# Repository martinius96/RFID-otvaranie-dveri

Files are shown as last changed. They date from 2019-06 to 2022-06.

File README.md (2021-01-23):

# RFID vrátnik s mikrokontrolérom ESP8266, ESP32
# Podporte projekt pre pridanie nových funkcionalít
* https://www.paypal.me/chlebovec
# Stránka projektu
* Informácie o projekte: http://arduino.clanweb.eu/rfid-system.php 
* Testovacie webové rozhranie: http://arduino.clanweb.eu/rfid/
* **Z dostupných zdrojových kódov pre platformy Arduino, ESP8266 a ESP32 je možné využiť iba HTTP variant, nakoľko freehosting clanweb.eu nemá podporu HTTPS!**
* Možnosť ihneď vyskúšať funkcionalitu systému v testovacom webovom rozhraní po zapojení čítačky NXP RC522 a nahratí programu pre odtestovanie funkčnosti
* Čítačka RC522 funguje na frekvencii 13.56 MHz, dokáže prečítať RFID tagy štandardu ISO/IEC 14443-A
* Webové rozhranie dokáže vizualizovať priloženia karty historicky s výsledkom overenia s možnosťou riadenia prístupu - autorizácie / deautorizácie kariet (automatická obnova údajov bola odstránená)
* Vhodné ako základ pre vlastný projekt s RFID vstupom od používateľa
* Pridaná podpora pre Over The Air aktualizáciu firmvéru prostredníctvom LAN siete - Basic OTA cez Python z prostredia Arduino IDE
* **Čítačka Wiegand, RDM6300 nie je dostupná vo free verzii projektu RFID vrátnik**
* Článok k projektu (verzia 1.0): https://chiptron.cz/articles.php?article_id=216

# Systém ponúka 2 typy užívateľov projektu
| Administrátor:  | Používateľ:  |
| --- | --- |
| Spravuje webové rozhranie | Fyzicky prikladá NFC tag/kľúčenku/náramok/kartu|
| V reálnom čase vidí priloženie karty s výsledkom overenia  | Pri overeni sú mu odistené dvere na 5 sekúnd|
| Historicky vidí 100 posledných priložení  | Pri neoverení používateľa sa jazýček nevtiahne  |
| Jedným kliknutím môže schváliť už (skôr) priloženú kartu  | Používateľ o overení/neoverení nie je informovaný (led/buzzer)|
| Odstránenie karty jedným kliknutím  |  Používateľ použije Mifare tag, bankomatovú kartu, ISIC kartu, náramok, ktorý spĺňa štandard ISO/IEC 14443 A |
| Grafická reprezentácia prístupov  | |
| Štatistika RFID vrátnika  |  |
| Vidí zdrojový kód pre mikrokontroléry  |  |

* Mikrokontróler po prečítaní UID (identifikátor, ktorý vysiela) RFID karty prostredníctvom čítačky odošle HTTP (HTTPS) POST request na webové rozhranie
* Webserver overí, či je karta medzi autorizovanými a odpovie textom OK, prípadne NO.
* Mikrokontróler na tento payload zareaguje a odistí dvere prostredníctvom solenoidu, ktorý je ovládaný cez 5V relé
* Z vnútornej strany objektu je možné dvere kľúčkou otvoriť, elektromagnetický jazýček (solenoid) sa vtiahne pri stlačení kľučky (1-cestný RFID vrátnik)
* Možno použiť Mifare tagy, ISIC karty, bankomatové, zamestnanecké karty, náramky i kľúčenky, ktoré spĺňajú štandard ISO/IEC 14443-A
* Mikrokontróler UID upraví, nikdy neodosiela pôvodný identifikátor karty, ktorý načíta.
* Na UART rozhranie mikrokontróler posiela udalosti - Eventy - priloženie karty s výsledkom overenia (akceptácie karty webserverom)
* UID sa ukladajú do MySQL databázy, existujú rôzne tabuľky - prístupy, autorizované karty, evidencia mien ku kartám...

# Hardvér
* NodeMCU**NodeMCU (v2, alebo v3)**
* BasekitBasekit (možný iba pri V3, možnosť využiť externé napájanie na 6-24V)
#
* Arduino Uno**Arduino Uno**
* Ethernet W5100Ethernet Wiznet W5100
* Ethernet W5500Ethernet Wiznet W5500
#
* ESP32 DevKit**ESP32 DevKit V1 / DevKitC V4**
#
* RC522Čítačka RC522 na 13.56 MHz pre štandard ISO/IEC 14443 A
* 13.56MHzKompatibilné karty a kľúčenky
* 1-kanálové elmg. reléSRD-05VDC-SL-C (elmg. relé 1-kanálové)
* Solenoidový jazýčekSolenoid - jazýčkový zámok

# Princíp solenoid jazýčka 
Princíp jazýčka

# Technológie
* HTML5
* PHP
* 
* 
* 
* Arduino core
* 

# Získanie Root CA certifikátu - (Pre ESP32 - HTTPS):
* openssl s_client -showcerts -verify 5 -connect example.com:443 < /dev/null
# Získanie SHA1 fingerprintu certifikátu - (Pre ESP8266 - HTTPS):
* openssl s_client -connect example.com:443 -showcerts < /dev/null 2>/dev/null   | openssl x509 -in /dev/stdin -sha1 -noout -fingerprint

# Inštalácia systému - krok po kroku
* Stiahnuť repozitár v .zip archíve z Githubu
* Súbor priečinka sql importovať do vašej MySQL databázy - štruktúru, alebo štruktúru + vzorové dáta
* V súbore connect.php nastaviť vaše údaje na databázu (umiestnenie (localhost/external), user, heslo, meno_db)
*  **(Win 10)** src priečinok skopírovať do: C:/Moje Dokumenty/Arduino/libraries/rfid
*  **(Win XP/Vista/7)** src priečinok skopírovať do: C:/Program Files/Arduino/libraries/rfid
* Web súbory nahrať na FTP server (kompatibilné s PHP 5, aj PHP 7)
* V zdrojovom kóde pre NodeMCU - zvoliť si verziu HTTPS/HTTP, zmeniť údaje k wifi sieti, údaje na váš webserver, rovnako i pre ESP32/Arduino
* Nahrať program, používať Arduino core 2.5.0/2.5.2 (pre NodeMCU), **verzia 2.3.0 (doteraz používaná) je nekompatibilná** pre HTTPS fingerprint!
* Pre Arduino, ESP32 je možné použiť aj nanovšie knižnice pre HTTP, HTTPS spojenia
* Program pre Arduino je plne kompatibilný medzi Arduino Uno, Nano, Mega 1280/2560
* Hotovo

# Webové rozhranie v prevádzke:
* Hlavný prehľad (real-time vstupy s výsledkom overenia)
Hlavný prehľad
* Pridanie autorizovaných kariet jedným kliknutím
Pridanie autorizovaných kariet jedným kliknutím
* Štatistika RFID vrátnika
Štatistika RFID vrátnika

# Zapojenie komponentov (Arduino)
| RC522 | Arduino |
|:-----|---:|
| 3.3V | 3.3V |
| RST  | D5 |
| GND  | GND |
| MISO | D12 |
| MOSI | D11 |
| SCK  | D5 |
| SDA/SS  | D6 |
| IRQ  | Nezapája sa |

| Relé | Arduino |
|:-----|---:|
| 5V | 5V  |
| GND  | GND |
| IN  | D3 |

# Zapojenie komponentov (NodeMCU)
| RC522 | NodeMCU |
|:-----|---:|
| 3.3V | 3.3V |
| RST  | D1 (GPIO5) |
| GND  | GND |
| MISO | D6 (GPIO12) |
| MOSI | D7 (GPIO13) |
| SCK  | D5 (GPIO14) |
| SDA/SS  | D2 (GPIO4) |
| IRQ  | Nezapája sa |

| Relé | NodeMCU |
|:-----|---:|
| 5V | VIN / VUSB (Adaptér/USB napájanie)  |
| GND  | GND |
| IN  | D0 (GPIO16) |

# Zapojenie komponentov (ESP32)
| RC522 | ESP32 |
|:-----|---:|
| 3.3V | 3.3V |
| RST  | D22 |
| GND  | GND |
| MISO | D19 |
| MOSI | D23 |
| SCK  | D18 |
| SDA/SS  | D21 |
| IRQ  | Nezapája sa |

| Relé | ESP32 |
|:-----|---:|
| 5V | 5V VIN  |
| GND  | GND |
| IN  | D17 |

# Zapojenie relé a solenoid jazyčkového zámku
| Relé | Solenoid |
|:-----|---:|
| NO | IN |
| COM  | - |
| NC  | 12/24 DC/AC |

* Nulák, respektíve GND podľa typu obvodu (AC/DC) je pripojený na zdroj po celú dobu prevádzky solenoid jazýčka.

# Schéma zapojenia Arduino
Schéma Arduino + Ethernet - RFID vrátnik

# Schéma zapojenia ESP8266 (NodeMCU)
Schéma NodeMCU - ESP8266 - RFID vrátnik

# Schéma zapojenia ESP32
Schéma ESP32 - RFID vrátnik

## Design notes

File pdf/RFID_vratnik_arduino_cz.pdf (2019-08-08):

# RFID SYSTÉM S ON-LINE SPRÁVOU V REÁLNOM ČASE

- 5.2.2019 ZBYŠEK VODA (https://arduino.cz/author/zbysekvoda/) ČLÁNKY, (https://arduino.cz/category/novinky/) ZAČÁTEČNÍK (https://arduino.cz/category/urovne/zacatecnik/) RFID (https://arduino.cz/tag/rfid/)

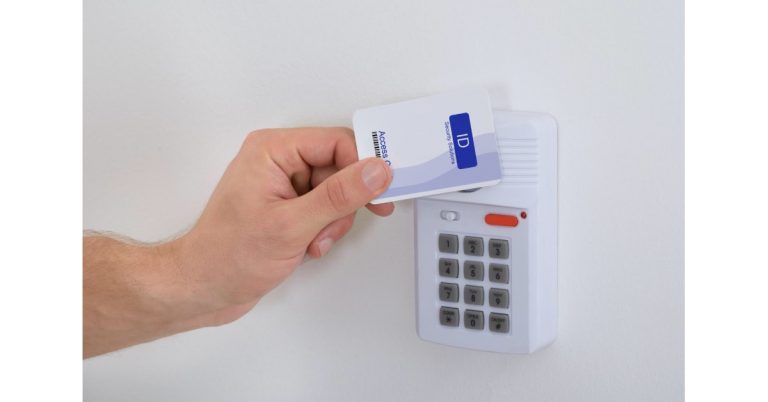
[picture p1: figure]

Ve dnešním článku se podíváme na přístupový systém založený na RFID kartách od našeho fanouška s přezdívkou martinius96.

Hledat … | H L E D A T
ÚVOD (https://arduino.cz/) | FÓRUM (https://www.arduino-forum.cz/) | ČLÁNKY (https://arduino.cz/category/novinky/) | CO JE TO ARDUINO? (https://arduino.cz/co-je-to-arduino/) | NÁVODY (https://arduino.cz/category/novinky/tutorialy/) | VIDEA (https://arduino.cz/category/videa/) | KOUPIT (https://www.hwkitchen.cz/arduino/)
Create PDF in your applications with the Pdfcrowd HTML to PDF API (https://pdfcrowd.com/doc/api/?ref=pdf) | PDFCROWD (https://pdfcrowd.com/?ref=pdf)

Zdar bastlíři, dnes by som rád predstavil systém, ktorý som vyvíjal pred niekoľkými mesiacmi.

Vyhotovil som RFID systém na otváranie dverí s elektomagnetickým jazýčekom na základe overenia užívateľa po priložení karty s takmer okamžitou odpoveďou. Systém je postavený na komponentoch pre Arduino, teda čítačka kariet a kľúčeniek na 13.56MHz RC522, kompatibilné karty a kľúčenky, relé. Tieto komponenty sú plne (https://www.hwkitchen.cz/rc522-rfid-ctecka-klicenka-a-karta/) kompatibilné aj s ESP modulmi. Rozhodol som sa pre NodeMCU s wi čipom ESP8266. (https://www.hwkitchen.cz/nodemcu-v3-esp8266-lua-wifi-ch340g/) Čítačka RC522 dokáže prečítať karty štandardu ISO/IEC 14443 A. Tento štandard funguje i na ISIC, bankomatové, autobusové, či zamestnanecké karty a je ich možné taktiež prečítať a využiť pre takýto projekt bez nutnosti investovať do nových kariet, či menších kľúčeniek. RC522 podporuje SPI zbernicu, po ktorej komunikuje s mikrokontrolérom.

## Aký je princíp funkčnosti tohto systému?

Čítačkou čítam MAC adresy kariet, ktoré si prevádzam na špecický decimálny formát (0-9 na každú pozíciu). Obsah karty sa nečíta! V úlohe mikrokontroléru pre spracovanie a odosielanie dát som použil dosku NodeMCU v3 Lolin, ktorá disponuje wi konektivitou, podporuje šifrovaný prenos a je pre tento účel je viac než dostačujúca.

Úlohou NodeMCU je odosielať dáta na web backend vždy, keď zaznamená kartu a na základe návratovej HTTP hlavičky určí podľa odpovede z webservera, či je užívateľovi povolený prístup. Dvere otvorí, alebo neotvorí, záznam s výsledkom si uloží do logu. Vo dverách sa okrem klasického mechanizmu s kľučkou nachádza i špeciálny elmg. jazýček, ktorý otvára mikrokontrolér na určitú dobu po úspešnej odpovedi z webservera. Funguje rovnako ako solenoid ventil. Nakoľko je na 5V a vyžaduje väčší prúd, využil som elektomagnetické relé na 3.3V so spínacím prúdom od 10mA (NodeMCU dáva 12mA na výstup), ktorým spínam mechanizmus jazýčka. Z vonkajšej strany dverí je guľa, z druhej strany kľučka, ktorá je prepojená i na jazýček. Z tohto dôvodu teda nie je nutné inštalovať dve čítačky, overuje sa iba užívateľ vchádzajúci do objektu.

Dáta sa odosielajú na server a spracúvajú sa na strane webservera v jazyku PHP. Všetky karty, ktoré boli kedy priložené sú archivované v MySQL databáze vrátane úspešných, alebo neúspešných overení používateľa vrátane času udalosti. Z administračného rozhrania, kde je možné vidieť i real-time vstupy do objektu je možné dané karty povoliť – autorizovať, alebo zamietnuť – deautorizovať. Real-time aktualizácia dát sa realizuje AJAX-ovým volaním.

Systém je rýchly a nastavenia pre karty na ich autorizáciu, alebo deautorizáciu je možné vykonať pohodlne odkiaľkoľvek jedným kliknutím. Je teda veľmi jednoduché takýto systém spravovať i pre laikov, ktorí nemajú skúsenosti. Systém je navrhnutý automatizovane. Administrátor sa iba stará o výber povolených – autorizovaných kariet, s ktorými je umožnený vstup do objektu. V prípade nedostupnosti webu/výpadku internetu je možné vždy do objektu vstúpiť kľúčom, ktorý dokáže jazýček odtiahnuť spolu s jazýčkom mechanizmu zámku.

## Môžem systém použiť? Sú zdrojové kódy dostupné?

Áno, systém je momentálne dostupný zdarma a je ho možné využívať. Systém je zbalený v repozitári na Github-e. Systém stačí rozbaliť, celú webovú časť nahrať na webserver, ktorý je pod HTTPS protokolom. Do MySQL databázy je nutné importovať tabuľky z sql priečinku repozitára a v súbore connect.php nastaviť údaje pre prístup do vašej databázy. Priamo vo web rozhraní je možné prezrieť si zdrojový kód pre mikrokontróler NodeMCU vrátane schémy zapojenia systému. Zdrojový kód je potrebné vhodne upraviť pre vaše použitie. Potrebujete zmeniť názov wi siete, na ktorú sa budete s ESP pripájať, zmeniť jej heslo, zmeniť webovú lokalitu, kde sa bude vykonávať HTTPS request po priložení karty. Pripojte RFID čítačku RC522 podľa priloženej schémy zapojenia, pripojte relé, pripojte svorkovicu relé na jazýček, nahrajte program a môžete ho využívať. V momentálnom nastavení budú dvere otvorené na 4 sekundy. Po uplynutí časť sa jazýček vystrčí, nakoľko má skosenú hranu, dvere je možné pribúchnuť a jazýček tak bezpečne zapadne do zárubne. Systém si môžete vhodne upraviť, pridať ďalšie zaujímavé prvky, napríklad buzzer, ktorý sa rozpípa pri priložení neautorizovanej karty. Niektoré elektronické zámky využívajú motorčeky pre jazýčky, ktoré je taktiež možné ovládať vhodným hardvérom.

Github repozitár s projektom je dostupný na: https://github.com/martinius96/RFID-otvaranie-dveri (https://github.com/martinius96/RFID-otvaranie-dveri)

Pre zaujímavosť datasheety čítačky a NodeMCU dosky:

Datasheet čítačky RC522: https://www.nxp.com/docs/en/data-sheet/MFRC522.pdf Datasheet NodeMCU (ESP8266): http://www.handsontec.com/pdf_learn/esp8266-V10.pdf (http://www.handsontec.com/pdf_learn/esp8266-V10.pdf)

Děkujeme za projekt. Máte i vy projekt, se kterým byste se chtěli pochlubit? Přečtěte si, jak na to. (https://arduino.cz/pochlubte-se-svym-arduino-projektem/)

## Napsat komentář

Pro přidávání komentářů se musíte nejdříve přihlásit. (https://arduino.cz/wp-login.php)

About | Latest Posts
| | používat novým způsobem.

Zbyšek Voda (https://arduino.cz/author/zbysekvoda/)
Už nějaký čas se zajímám o věci kolem Internetu věcí a otevřeného hardware a software. Tak jsem se také v roce 2010 dostal k Arduinu, pro které dodnes programuji a taky píšu články o práci s ním. Baví mě vymýšlet, jak staré věci

P Ř I H L Á S I T S E (https://arduino.cz/wp-login.php) | I N F O @ A R D U I N O . C Z |
A R D U I N O . C Z 2 0 1 4 - 2 0 1 9
P O W E R E D B Y H W K I T C H E N . C Z (https://www.hwkitchen.cz/)

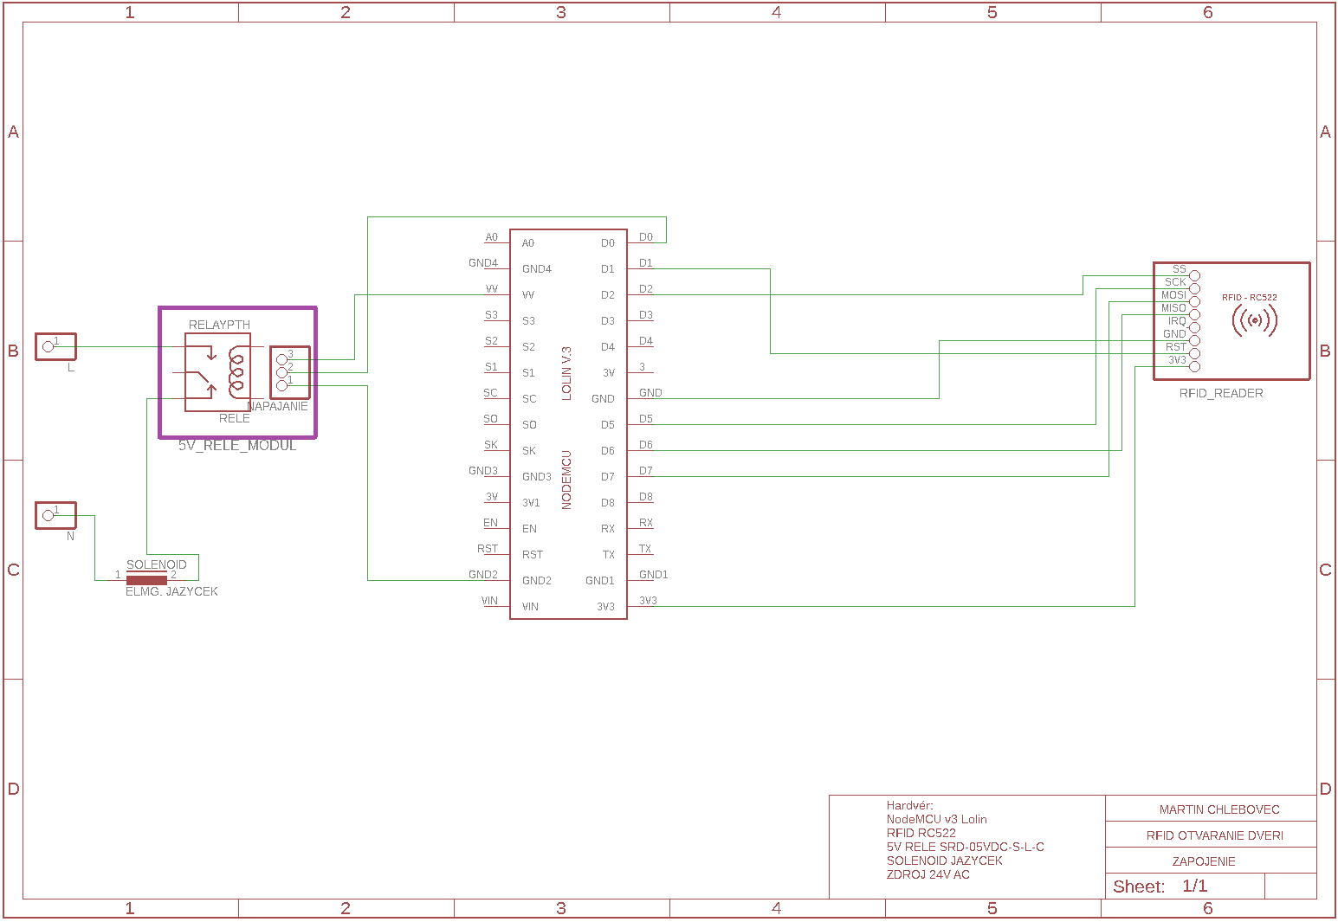
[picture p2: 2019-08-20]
eagle/ESP8266/rfid_otvaranie_dveri.png

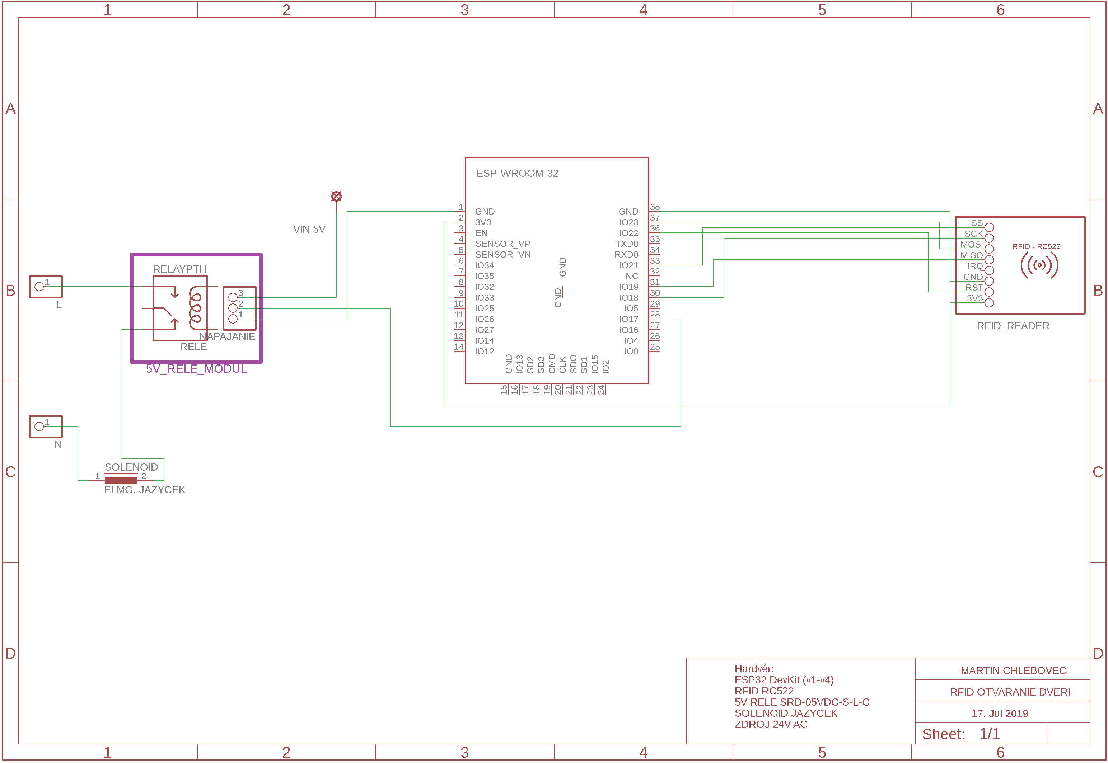
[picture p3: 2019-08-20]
eagle/ESP32/rfid_otvaranie_dveri_esp32.png

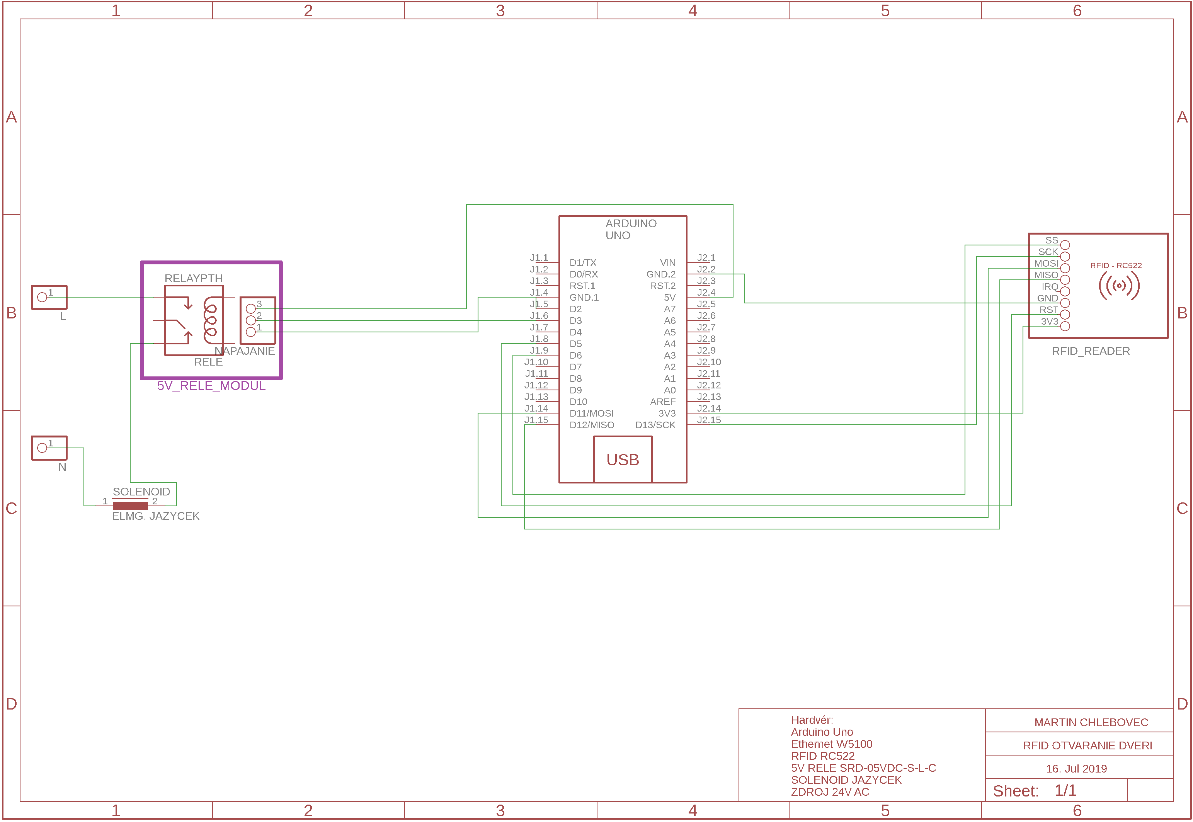
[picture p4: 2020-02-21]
eagle/Arduino/rfid_ethernet.png

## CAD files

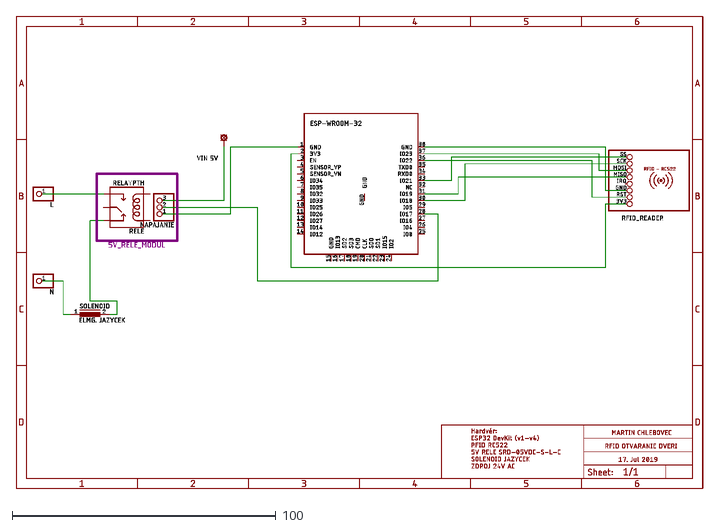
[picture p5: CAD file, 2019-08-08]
eagle/ESP32/rfid_vratnik_esp32.dxf
260.6 x 179.4

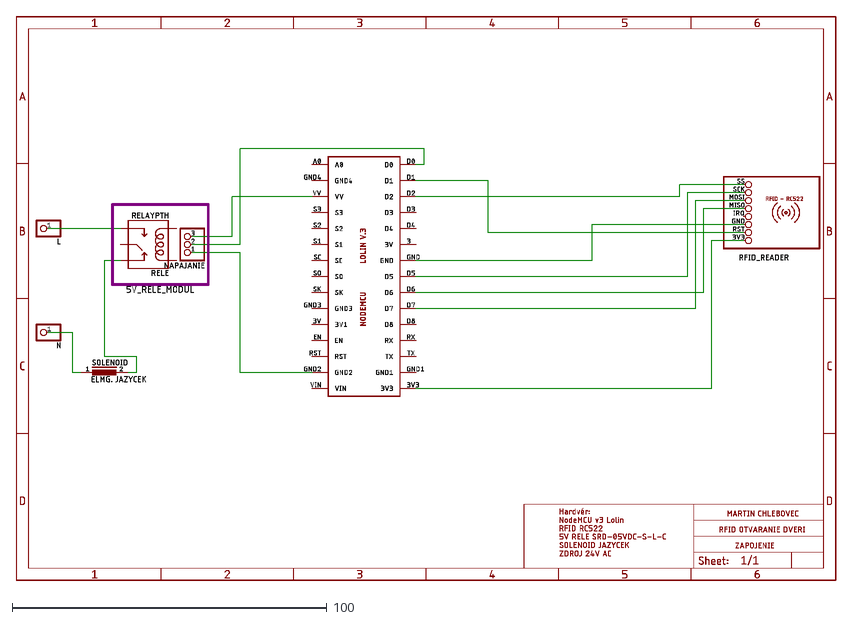
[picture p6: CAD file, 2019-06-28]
eagle/ESP8266/rfid_vratnik_esp8266.dxf
260.6 x 179.4

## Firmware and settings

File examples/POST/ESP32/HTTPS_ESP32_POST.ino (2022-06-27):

/*|--------------------------------------------------------|*/
/*|Project: RFID remote database access webapp             |*/
/*|ESP32 (DevKit, Generic), Arduino Core with FreeRTOS     |*/
/*|Autor: Martin Chlebovec (martinius96)                   |*/
/*|E-mail: martinius96@gmail.com                           |*/
/*|Usage license: MIT                                      |*/
/*|Revision: 31. March 2022                                |*/
/*|Tested stable ESP32 core: 2.0.1 / 2.0.3-RC1 (IDF 4.4)   |*/
/*|799 kB flash usage, 38 kB RAM usage                     |*/
/*|WEB: https://hladinomer.000webhostapp.com/rfid/         |*/
/*|--------------------------------------------------------|*/

#include <WiFi.h>
#include <WiFiClientSecure.h>
#include <SPI.h>
#include <MFRC522.h>

unsigned long code;
const int rele = 17; //RELAY PIN
#define SS_PIN 21 //CHIP SELECT PIN
#define RST_PIN 22 //RESET PIN

const char * ssid = "MY_WIFI"; //WiFi hotspot name
const char * password = "MY_WIFI_PASSWORD"; //WiFi hotspot password
const char* host = "hladinomer.000webhostapp.com"; //domain - host
String url = "/rfid/karta.php"; //URL behind host domain --> target PHP file



TaskHandle_t Task1; //ULTRASONIC MEASUREMENT
TaskHandle_t Task2; //WIFI HTTP SOCKET
QueueHandle_t  q = NULL;

WiFiClientSecure client;
MFRC522 rfid(SS_PIN, RST_PIN);
static void Task1code( void * parameter);
static void Task2code( void * parameter);
void dump_byte_array(byte *buffer, byte bufferSize);

//DST ROOT CA X3 EXAMPLE (https://i.imgur.com/fvw4huT.png)
const static char* test_root_ca PROGMEM = \
    "-----BEGIN CERTIFICATE-----\n" \
    "MIIDrzCCApegAwIBAgIQCDvgVpBCRrGhdWrJWZHHSjANBgkqhkiG9w0BAQUFADBh\n" \
    "MQswCQYDVQQGEwJVUzEVMBMGA1UEChMMRGlnaUNlcnQgSW5jMRkwFwYDVQQLExB3\n" \
    "d3cuZGlnaWNlcnQuY29tMSAwHgYDVQQDExdEaWdpQ2VydCBHbG9iYWwgUm9vdCBD\n" \
    "QTAeFw0wNjExMTAwMDAwMDBaFw0zMTExMTAwMDAwMDBaMGExCzAJBgNVBAYTAlVT\n" \
    "MRUwEwYDVQQKEwxEaWdpQ2VydCBJbmMxGTAXBgNVBAsTEHd3dy5kaWdpY2VydC5j\n" \
    "b20xIDAeBgNVBAMTF0RpZ2lDZXJ0IEdsb2JhbCBSb290IENBMIIBIjANBgkqhkiG\n" \
    "9w0BAQEFAAOCAQ8AMIIBCgKCAQEA4jvhEXLeqKTTo1eqUKKPC3eQyaKl7hLOllsB\n" \
    "CSDMAZOnTjC3U/dDxGkAV53ijSLdhwZAAIEJzs4bg7/fzTtxRuLWZscFs3YnFo97\n" \
    "nh6Vfe63SKMI2tavegw5BmV/Sl0fvBf4q77uKNd0f3p4mVmFaG5cIzJLv07A6Fpt\n" \
    "43C/dxC//AH2hdmoRBBYMql1GNXRor5H4idq9Joz+EkIYIvUX7Q6hL+hqkpMfT7P\n" \
    "T19sdl6gSzeRntwi5m3OFBqOasv+zbMUZBfHWymeMr/y7vrTC0LUq7dBMtoM1O/4\n" \
    "gdW7jVg/tRvoSSiicNoxBN33shbyTApOB6jtSj1etX+jkMOvJwIDAQABo2MwYTAO\n" \
    "BgNVHQ8BAf8EBAMCAYYwDwYDVR0TAQH/BAUwAwEB/zAdBgNVHQ4EFgQUA95QNVbR\n" \
    "TLtm8KPiGxvDl7I90VUwHwYDVR0jBBgwFoAUA95QNVbRTLtm8KPiGxvDl7I90VUw\n" \
    "DQYJKoZIhvcNAQEFBQADggEBAMucN6pIExIK+t1EnE9SsPTfrgT1eXkIoyQY/Esr\n" \
    "hMAtudXH/vTBH1jLuG2cenTnmCmrEbXjcKChzUyImZOMkXDiqw8cvpOp/2PV5Adg\n" \
    "06O/nVsJ8dWO41P0jmP6P6fbtGbfYmbW0W5BjfIttep3Sp+dWOIrWcBAI+0tKIJF\n" \
    "PnlUkiaY4IBIqDfv8NZ5YBberOgOzW6sRBc4L0na4UU+Krk2U886UAb3LujEV0ls\n" \
    "YSEY1QSteDwsOoBrp+uvFRTp2InBuThs4pFsiv9kuXclVzDAGySj4dzp30d8tbQk\n" \
    "CAUw7C29C79Fv1C5qfPrmAESrciIxpg0X40KPMbp1ZWVbd4=\n" \
    "-----END CERTIFICATE-----\n";

void setup() {
  Serial.begin(115200);
  SPI.begin();
  rfid.PCD_Init(); // Init MFRC522
  rfid.PCD_SetAntennaGain(112); // set antenna gain to max (00001110)
  rfid.PCD_DumpVersionToSerial(); //Write version of Firmware to UART
  pinMode(rele, OUTPUT);
  digitalWrite(rele, HIGH); //hotfix
  WiFi.begin(ssid, password); //pripoj sa na wifi siet s heslom
  while (WiFi.status() != WL_CONNECTED) {
    delay(500);
    Serial.print(".");
  }
  Serial.println(F(""));
  Serial.println(F("Wifi connected with IP:"));
  Serial.println(WiFi.localIP());
  client.setCACert(test_root_ca);
  q = xQueueCreate(20, sizeof(unsigned long));
  if (q != NULL) {
    Serial.println(F("Queue FIFO buffer is created"));
    vTaskDelay(1000 / portTICK_PERIOD_MS); //wait for a second
    xTaskCreatePinnedToCore(
      Task1code,   /* Task function. */
      "Task1",     /* name of task. */
      10000,       /* Stack size of task */
      NULL,        /* parameter of the task */
      1,           /* priority of the task */
      &Task1,      /* Task handle to keep track of created task */
      1);          /* pin task to core 1 */
    Serial.println(F("RFID handler task started"));
    xTaskCreatePinnedToCore(
      Task2code,   /* Task function. */
      "Task2",     /* name of task. */
      10000,       /* Stack size of task */
      NULL,        /* parameter of the task */
      1,           /* priority of the task */
      &Task2,      /* Task handle to keep track of created task */
      0);          /* pin task to core 0 */
    Serial.println(F("HTTP Socket task started"));
  } else {
    Serial.println(F("Queue creation failed"));
  }
}

void loop() {
  if (WiFi.status() != WL_CONNECTED) {
    WiFi.begin(ssid, password); //pripoj sa na wifi siet s heslom
  }
  while (WiFi.status() != WL_CONNECTED) {
    delay(500);
    Serial.print(".");
  }
  yield();

}

static void Task1code( void * parameter) {
  unsigned long RFIDcode;
  if (q == NULL) {
    Serial.println(F("Queue in RFID handler task is not ready"));
    return;
  }
  while (1) {
    if (rfid.PICC_IsNewCardPresent() && rfid.PICC_ReadCardSerial()) {
      dump_byte_array(rfid.uid.uidByte, rfid.uid.size);
      rfid.PICC_HaltA();
      rfid.PCD_StopCrypto1();
      RFIDcode = code;
      xQueueSend(q, (void *)&RFIDcode, (TickType_t )0); //add the measurement value to Queue
    }
  }
}
static void Task2code( void * parameter) {
  unsigned long RFIDcode;
  if (q == NULL) {
    Serial.println(F("Queue in HTTP socket task is not ready"));
    return;
  }
  while (1) {
    xQueueReceive(q, &RFIDcode, portMAX_DELAY); //read measurement value from Queue and run code below, if no value, WAIT until portMAX_DELAY
    String data = "kod=" + RFIDcode;
    if (client.connect(host, 443)) {
      client.println("POST " + url + " HTTP/1.0");
      client.println("Host: " + (String)host);
      client.println("User-Agent: ESP32");
      client.println("Connection: close");
      client.println("Content-Type: application/x-www-form-urlencoded;");
      client.print("Content-Length: ");
      client.println(data.length());
      client.println();
      client.println(data);
      while (client.connected()) {
        String line = client.readStringUntil('\n');
        if (line == "\r") {
          break;
        }
      }
      String line = client.readStringUntil('\n');
      if (line.indexOf("OK") > 0) {
        Serial.println(F("ACCESS GAINED"));
        Serial.println(F("DOORS OPENED"));
        digitalWrite(rele, LOW); //inverted ACTIVE-LOW logic
        delay(5500);              //duration of doors opened
        digitalWrite(rele, HIGH); //lock doors pack
        Serial.println(F("DOORS CLOSED"));
      } else if (line.indexOf("NO") > 0) {
        Serial.println(F("ACCESS REJECTED"));
      } else {
        Serial.println(F("WAIT 5 seconds before next attempt!"));
      }
    } else {
      Serial.println(F("Connection to webserver was not successful!"));
    }
    client.stop();
  }
}

void dump_byte_array(byte *buffer, byte bufferSize) {
  for (byte i = 0; i < bufferSize; i++) {
  }
  Serial.print(F("Detected UID (code) of RFID CARD: "));
  code = 10000 * buffer[4] + 1000 * buffer[3] + 100 * buffer[2] + 10 * buffer[1] + buffer[0]; //finalny kod karty
  Serial.println(code);
}

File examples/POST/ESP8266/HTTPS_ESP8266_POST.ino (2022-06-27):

/*|----------------------------------------------------------|*/
/*|SKETCH PRE RFID SYSTEM S WEB ADMINISTRACIOU               |*/
/*|VYHOTOVIL: MARTIN CHLEBOVEC                               |*/
/*|FB: https://www.facebook.com/martin.s.chlebovec           |*/
/*|EMAIL: martinius96@gmail.com                              |*/
/*|Doska: NodeMCU v3 Lolin (v2 compatible), Wemos D1 Mini    |*/
/*|CORE: 3.0.0+                                              |*/
/*|WEB: https://hladinomer.000webhostapp.com/rfid/           |*/
/*|----------------------------------------------------------|*/
//#define OTA //odkomentuj pre OTA UPDATE CEZ LAN z Arduino IDE (espota.py)
#include <Arduino.h>             // Arduino core
#include <ESP8266WiFi.h>
#include <WiFiClientSecure.h>
#include <SPI.h>
#include <RFID.h>

#ifdef OTA
#include <ESP8266mDNS.h>
#include <WiFiUdp.h>
#include <ArduinoOTA.h>
#endif
WiFiClientSecure client;

//WIFI RELATED
const char * ssid = "WIFI_NAME";
const char * password = "WIFI_PASSWORD";


//WEBSERVER RELATED
const char* host = "hladinomer.000webhostapp.com"; //domain - host
String url = "/rfid/karta.php"; //URL behind host domain --> target PHP file
const int httpsPort = 443; //https port

const int rele = 16; //GPIO16 == D0
//Root CA cert --> CERTIFIKÁT CERTIFIKAČNEJ AUTORITY, KTORÁ VYDALA CERTIFIKÁT VÁŠ WEBSERVER v .pem formáte
//DST ROOT CA X3 EXAMPLE (https://i.imgur.com/fvw4huT.png)
const static char* test_root_ca PROGMEM = \
    "-----BEGIN CERTIFICATE-----\n" \
    "MIIDrzCCApegAwIBAgIQCDvgVpBCRrGhdWrJWZHHSjANBgkqhkiG9w0BAQUFADBh\n" \
    "MQswCQYDVQQGEwJVUzEVMBMGA1UEChMMRGlnaUNlcnQgSW5jMRkwFwYDVQQLExB3\n" \
    "d3cuZGlnaWNlcnQuY29tMSAwHgYDVQQDExdEaWdpQ2VydCBHbG9iYWwgUm9vdCBD\n" \
    "QTAeFw0wNjExMTAwMDAwMDBaFw0zMTExMTAwMDAwMDBaMGExCzAJBgNVBAYTAlVT\n" \
    "MRUwEwYDVQQKEwxEaWdpQ2VydCBJbmMxGTAXBgNVBAsTEHd3dy5kaWdpY2VydC5j\n" \
    "b20xIDAeBgNVBAMTF0RpZ2lDZXJ0IEdsb2JhbCBSb290IENBMIIBIjANBgkqhkiG\n" \
    "9w0BAQEFAAOCAQ8AMIIBCgKCAQEA4jvhEXLeqKTTo1eqUKKPC3eQyaKl7hLOllsB\n" \
    "CSDMAZOnTjC3U/dDxGkAV53ijSLdhwZAAIEJzs4bg7/fzTtxRuLWZscFs3YnFo97\n" \
    "nh6Vfe63SKMI2tavegw5BmV/Sl0fvBf4q77uKNd0f3p4mVmFaG5cIzJLv07A6Fpt\n" \
    "43C/dxC//AH2hdmoRBBYMql1GNXRor5H4idq9Joz+EkIYIvUX7Q6hL+hqkpMfT7P\n" \
    "T19sdl6gSzeRntwi5m3OFBqOasv+zbMUZBfHWymeMr/y7vrTC0LUq7dBMtoM1O/4\n" \
    "gdW7jVg/tRvoSSiicNoxBN33shbyTApOB6jtSj1etX+jkMOvJwIDAQABo2MwYTAO\n" \
    "BgNVHQ8BAf8EBAMCAYYwDwYDVR0TAQH/BAUwAwEB/zAdBgNVHQ4EFgQUA95QNVbR\n" \
    "TLtm8KPiGxvDl7I90VUwHwYDVR0jBBgwFoAUA95QNVbRTLtm8KPiGxvDl7I90VUw\n" \
    "DQYJKoZIhvcNAQEFBQADggEBAMucN6pIExIK+t1EnE9SsPTfrgT1eXkIoyQY/Esr\n" \
    "hMAtudXH/vTBH1jLuG2cenTnmCmrEbXjcKChzUyImZOMkXDiqw8cvpOp/2PV5Adg\n" \
    "06O/nVsJ8dWO41P0jmP6P6fbtGbfYmbW0W5BjfIttep3Sp+dWOIrWcBAI+0tKIJF\n" \
    "PnlUkiaY4IBIqDfv8NZ5YBberOgOzW6sRBc4L0na4UU+Krk2U886UAb3LujEV0ls\n" \
    "YSEY1QSteDwsOoBrp+uvFRTp2InBuThs4pFsiv9kuXclVzDAGySj4dzp30d8tbQk\n" \
    "CAUw7C29C79Fv1C5qfPrmAESrciIxpg0X40KPMbp1ZWVbd4=\n" \
    "-----END CERTIFICATE-----\n";
X509List cert(test_root_ca);
#define SS_PIN 4 //D2
#define RST_PIN 5 //D1
RFID rfid(SS_PIN, RST_PIN);
unsigned long kod;

void setup() {
  Serial.begin(9600);
  SPI.begin();
  rfid.init();
  pinMode(rele, OUTPUT);
  digitalWrite(rele, HIGH); //hotfix
  WiFi.begin(ssid, password);
  while (WiFi.status() != WL_CONNECTED) {
    delay(500);
    Serial.print(".");
  }
#ifdef OTA
  // Port defaults to 8266
  // ArduinoOTA.setPort(8266);

  // Hostname defaults to esp8266-[ChipID]
  // ArduinoOTA.setHostname("myesp8266");

  // No authentication by default
  // ArduinoOTA.setPassword((const char *)"123");

  ArduinoOTA.onStart([]() {
    Serial.println("Start");
  });
  ArduinoOTA.onEnd([]() {
    Serial.println("\nEnd");
  });
  ArduinoOTA.onProgress([](unsigned int progress, unsigned int total) {
    Serial.printf("Progress: %u%%\r", (progress / (total / 100)));
  });
  ArduinoOTA.onError([](ota_error_t error) {
    Serial.printf("Error[%u]: ", error);
    if (error == OTA_AUTH_ERROR) Serial.println("Auth Failed");
    else if (error == OTA_BEGIN_ERROR) Serial.println("Begin Failed");
    else if (error == OTA_CONNECT_ERROR) Serial.println("Connect Failed");
    else if (error == OTA_RECEIVE_ERROR) Serial.println("Receive Failed");
    else if (error == OTA_END_ERROR) Serial.println("End Failed");
  });
  ArduinoOTA.begin();
#endif
  Serial.println("");
  Serial.println("WiFi uspesne pripojene");
  Serial.println("IP adresa: ");
  Serial.println(WiFi.localIP());
  // Set time via NTP, as required for x.509 validation
  configTime(3 * 3600, 0, "pool.ntp.org", "time.nist.gov");

  Serial.print("Waiting for NTP time sync: ");
  time_t now = time(nullptr);
  while (now < 8 * 3600 * 2) {
    delay(500);
    Serial.print(".");
    now = time(nullptr);
  }
  Serial.println("");
  struct tm timeinfo;
  gmtime_r(&now, &timeinfo);
  Serial.print("Current time: ");
  Serial.print(asctime(&timeinfo));
  Serial.printf("Using certificate: %s\n", test_root_ca);
  client.setTrustAnchors(&cert);
  Serial.println("Ready");
}

void loop() {
  if (WiFi.status() != WL_CONNECTED) {
    WiFi.begin(ssid, password);
  }
  while (WiFi.status() != WL_CONNECTED) {
    delay(500);
    Serial.print(".");
  }
yield();
#ifdef OTA
  ArduinoOTA.handle();
#endif
  if (rfid.isCard()) {
    if (rfid.readCardSerial()) {
      Serial.println(" ");
      Serial.println("Card found");
      kod = 10000 * rfid.serNum[4] + 1000 * rfid.serNum[3] + 100 * rfid.serNum[2] + 10 * rfid.serNum[1] + rfid.serNum[0];
      Serial.println(kod);
      String kodik = String(kod);
      String data = "kod=" + kodik;
      if (client.connect(host, httpsPort)) {
        client.println("POST " + url + " HTTP/1.0");
        client.println("Host: " + (String)host);
        client.println("User-Agent: ESP8266");
        client.println("Connection: close");
        client.println("Content-Type: application/x-www-form-urlencoded;");
        client.print("Content-Length: ");
        client.println(data.length());
        client.println();
        client.println(data);
        while (client.connected()) {
          String line = client.readStringUntil('\n');
          if (line == "\r") {
            break;
          }
        }
        String line = client.readStringUntil('\n');
        if (line.indexOf("OK") > 0) {
          Serial.println(F("VSTUP POVOLENY"));
          Serial.println(F("DVERE ODOMKNUTE"));
          digitalWrite(rele, LOW); //invertovane spinane rele active LOW
          delay(5500);              //cas otvorenia dveri
          digitalWrite(rele, HIGH); //zatvor zamok
          Serial.println(F("DVERE ZAMKNUTE"));
        } else if (line.indexOf("NO") > 0) {
          Serial.println(F("VSTUP ZAMIETNUTY"));
        } else {
          Serial.println(F("Prosim pockajte s dalsim overenim karty 5 sekund!"));
        }
      }
      client.stop();
    }
  }
  rfid.halt();
}

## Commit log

2019-06-25 odstranenie projektu pred porusovatelmi licencie
    [data.csv]
2019-06-28 upraveny system s monitorovanim poruseni licencie
    [data.csv, struktura.csv, struktura_a_vzorove_data.csv]
2019-07-16 schemy pre UNO
    [rozrobene_rfid_uno.dxf, rozrobene_rfid_uno.sch]
2019-07-17 esp32 subory pre Eagle
    [rozrobene_rfid_esp32.dxf, rozrobene_rfid_esp32.sch]
2019-07-17 esp32 sketch
2019-08-07 hotfix pre ESP32 - viacnasobny request za 1 sek.
2020-03-24 uprava podľa schemy pre Arduino
2020-03-24 program pre Arduino
2020-04-15 zmena fingerprintu
2020-08-23 get Root CA cert + get SHA1 fingerprint
2022-06-23 fixed undefined reference to loop
    [HTTPS_ESP8266_POST.ino]
